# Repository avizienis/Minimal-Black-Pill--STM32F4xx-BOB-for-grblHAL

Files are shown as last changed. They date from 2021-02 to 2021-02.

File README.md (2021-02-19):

# Minimal Black Pill (STM32F4xx) BOB for grblHAL 
Single layer breakout board for the popular Black Pill (*NOT Blue Pill*). Features 4 axes, 5V outputs, optoisolated inputs.

Firmware: [grblHAL](https://github.com/terjeio/grblHAL)

The goal of this project was to replace a classical Grbl setup on an Arduino Uno/Nano, with minimal effort and minimal features (which is enough for most hobby machines anyway).
All inputs are mapped to one side of the board, all outputs (except spindle PWM) are on the other. 
This allows for a very clean single sided design and is very suitable milling, UV exposing or even toner transfer methods.
The only critical requirements for manufacturing - minimal separation between traces is 0.2mm.

## Feb 2021 Initial release
  * 4 Axis outputs
  * 10 5V buffered outputs (XYZA step/dir outputs, single source-multiple buffered outputs enable, spindle PWM and enable, mist, flood)  
  * 8 Opto-isolated inputs (mapped to XYZ limits, probe, halt, pause, start, safety door)
  * External supply connectors. Can be powered by USB, external 5V or external 12V-24V (depending on the Vreg). 
  * All I/O done on 3.5mm pitch connectors.
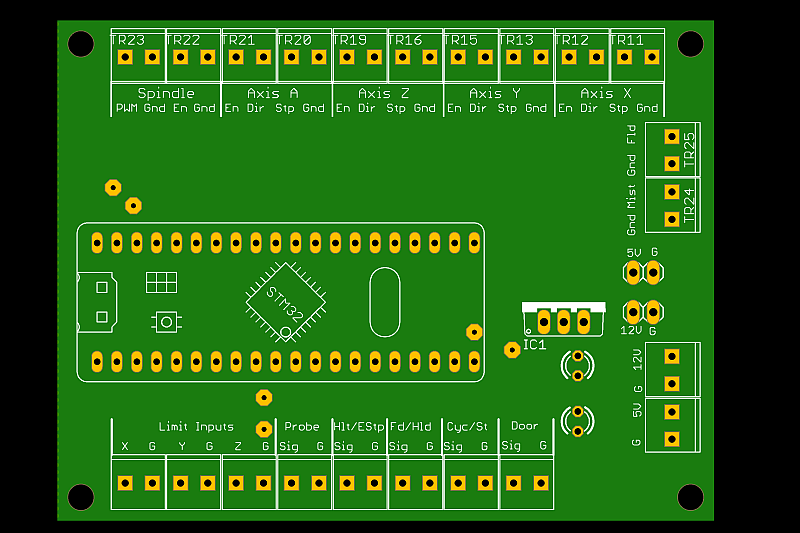
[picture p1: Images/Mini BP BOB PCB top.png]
Top view

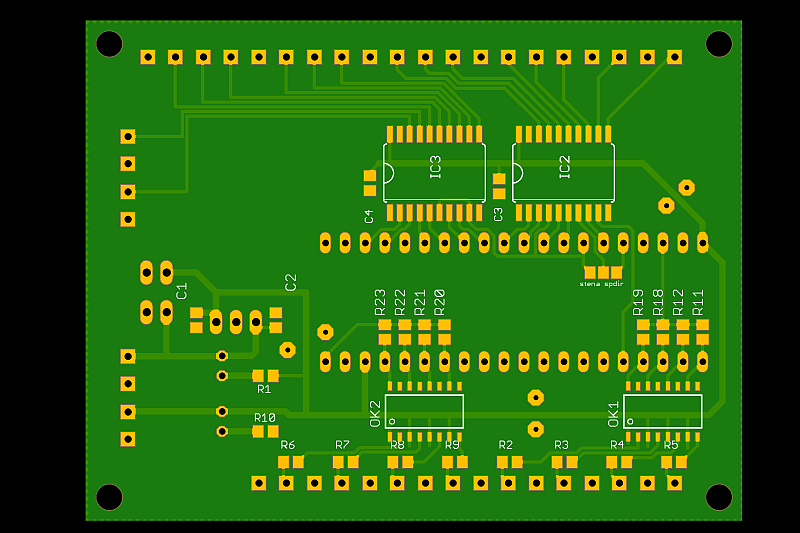
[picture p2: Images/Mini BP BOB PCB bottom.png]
Bottom view

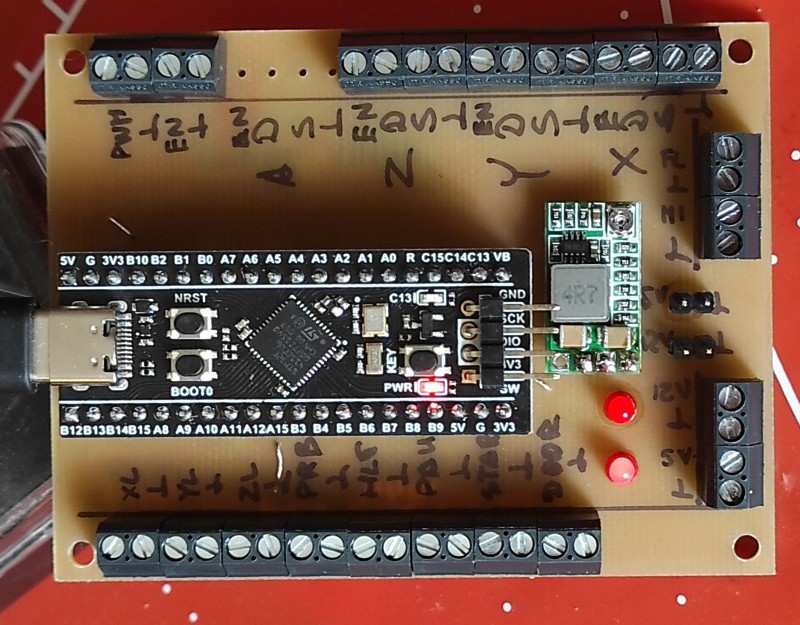
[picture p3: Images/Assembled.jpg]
Assembled

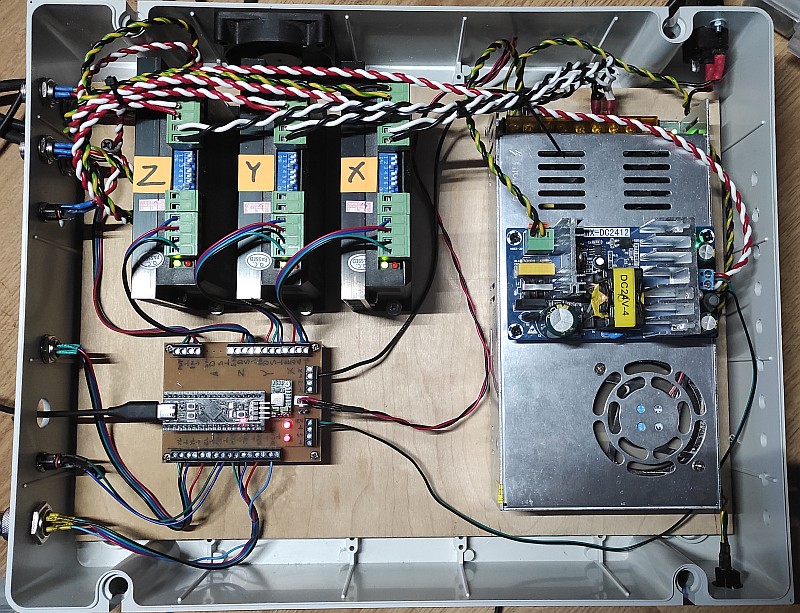
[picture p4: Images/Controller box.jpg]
Control box


## Notes

### Vreg can be a simple 7805 or as in my implementation (also see images folder) - a tiny DC-DC converter. The latter happily accepts up to 24V input.
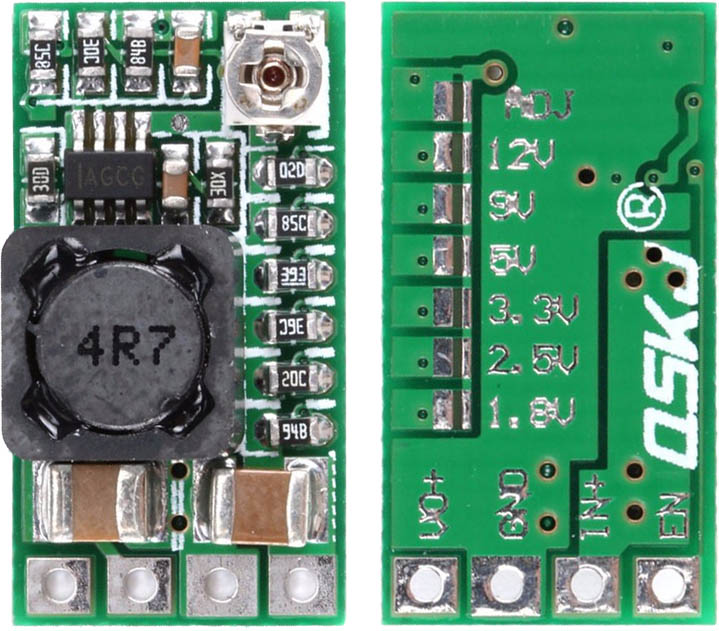
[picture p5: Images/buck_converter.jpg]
DC-DC converter


### This is only tested on genuine [WeAct Black Pill V3](https://github.com/WeActTC/MiniF4-STM32F4x1).
Other/older versions of the board can have slightly different mappings.
Also I've read that blocking USB power diodes are not present on some older variants of the board.
If so, when using external supply microcontroller's 5V lines should not be connected to the main board.

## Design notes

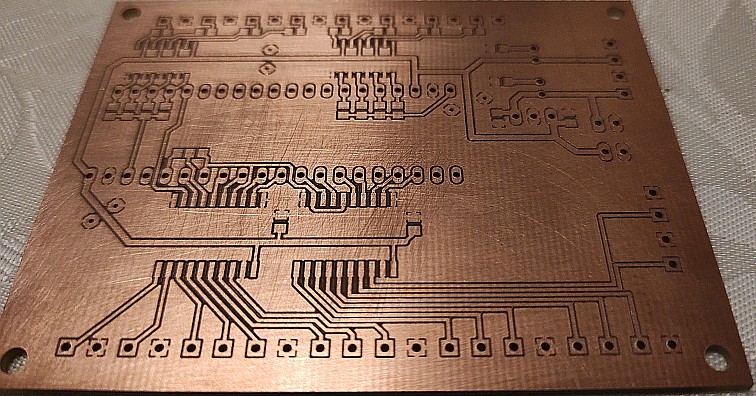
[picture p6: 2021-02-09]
Images/milled_pcb.jpg

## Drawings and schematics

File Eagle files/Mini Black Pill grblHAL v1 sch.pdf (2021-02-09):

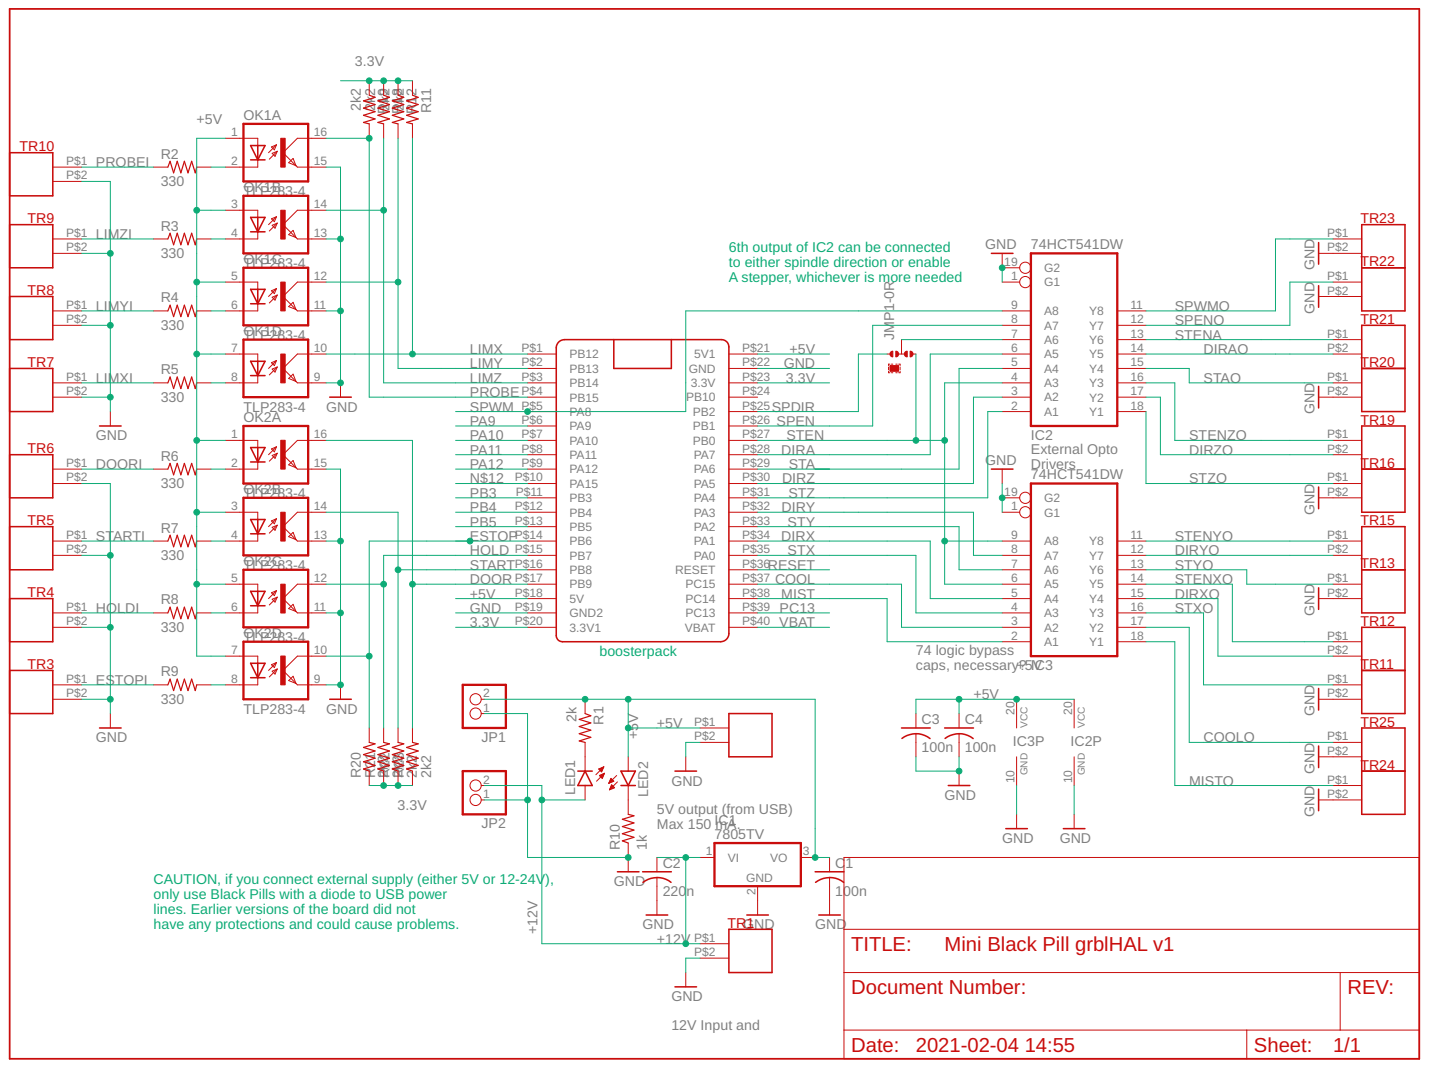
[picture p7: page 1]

6th output of IC2 can be connected
to either spindle direction or enable A stepper, whichever is more needed

CAUTION, if you connect external supply (either 5V or 12-24V), only use Black Pills with a diode to USB power

lines. Earlier versions of the board did not
have any protections and could cause problems.

Mini Black Pill grblHAL v1

Document Number: | REV:

Date: 2021-02-04 14:55 | Sheet: 1/1

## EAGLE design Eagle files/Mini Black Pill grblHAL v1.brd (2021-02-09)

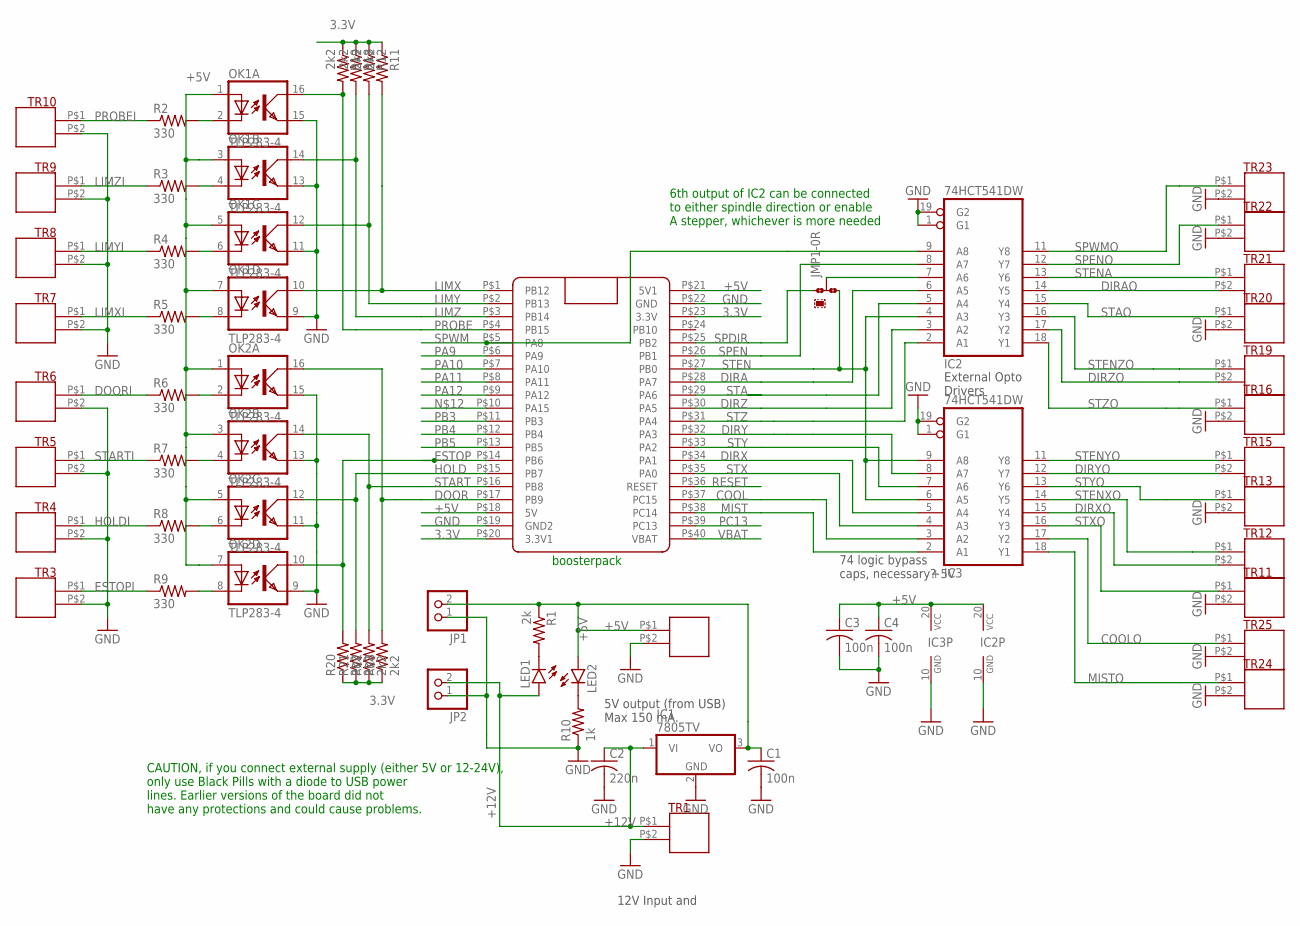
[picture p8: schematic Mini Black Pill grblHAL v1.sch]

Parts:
C1, C3, C4: 100n; C0805
C2: 220n; C0805
IC1: 7805TV; TO220V
IC2, IC3: 74HCT541DW; SO20W
JMP1: 0R-JUMPA; A0R-JMP
JP1, JP2: PINHD-1X2; 1X02
LED1, LED2: LED3MM
OK1, OK2: TLP283-4; MINI-FLAT-16
R1: 2k; R0805
R2, R3, R4, R5, R6, R7, R8, R9: 330; R0805
R10: 1k; R0805
R11, R12, R18, R19, R20, R21, R22, R23: 2k2; R0805
TR1, TR2, TR3, TR4, TR5, TR6, TR7, TR8, TR9, TR10, TR11, TR12, TR13, TR15, TR16, TR19, TR20, TR21, TR22, TR23, TR24, TR25: T35-2
U$2: BLACK_PILL; BLUE_PILL

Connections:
3.3V: R11.1, R12.1, R18.1, R19.1, R20.1, R21.1, R22.1, R23.1, U$2.P$20 (3.3V1), U$2.P$23 (3.3V)
+5V: C1.1, C3.1, C4.1, IC1.3 (VO), IC2.20 (VCC), IC3.20 (VCC), JP1.2, LED2.A, OK1.1 (A), OK1.3 (A), OK1.5 (A), OK1.7 (A), OK2.1 (A), OK2.3 (A), OK2.5 (A), OK2.7 (A), R1.1, TR2.P$1, U$2.P$18 (5V), U$2.P$21 (5V1)
+12V: C2.1, IC1.1 (VI), JP2.2, LED1.A, TR1.P$1
COOL: IC3.3 (A2), U$2.P$37 (PC15)
COOLO: IC3.17 (Y2), TR25.P$1
DIRA: IC2.6 (A5), U$2.P$28 (PA7)
DIRAO: IC2.14 (Y5), TR21.P$2
DIRX: IC3.5 (A4), U$2.P$34 (PA1)
DIRXO: IC3.15 (Y4), TR12.P$2
DIRY: IC3.8 (A7), U$2.P$32 (PA3)
DIRYO: IC3.12 (Y7), TR15.P$2
DIRZ: IC2.3 (A2), U$2.P$30 (PA5)
DIRZO: IC2.17 (Y2), TR19.P$2
DOOR: OK2.16 (COL), R23.2, U$2.P$17 (PB9)
DOORI: R6.1, TR6.P$1
ESTOP: OK2.10 (COL), R20.2, U$2.P$14 (PB6)
ESTOPI: R9.1, TR3.P$1
GND: C1.2, C2.2, C3.2, C4.2, IC1.2 (GND), IC2.1 (G1), IC2.10 (GND), IC2.19 (G2), IC3.1 (G1), IC3.10 (GND), IC3.19 (G2), JP1.1, JP2.1, OK1.9 (EMIT), OK1.11 (EMIT), OK1.13 (EMIT), OK1.15 (EMIT), OK2.9 (EMIT), OK2.11 (EMIT), OK2.13 (EMIT), OK2.15 (EMIT), R10.1, TR1.P$2, TR2.P$2, TR3.P$2, TR4.P$2, TR5.P$2, TR6.P$2, TR7.P$2, TR8.P$2, TR9.P$2, TR10.P$2, TR11.P$2, TR13.P$2, TR16.P$2, TR20.P$2, TR22.P$2, TR23.P$2, TR24.P$2, TR25.P$2, U$2.P$19 (GND2), U$2.P$22 (GND)
HOLD: OK2.12 (COL), R21.2, U$2.P$15 (PB7)
HOLDI: R8.1, TR4.P$1
LIMX: OK1.10 (COL), R11.2, U$2.P$1 (PB12)
LIMXI: R5.1, TR7.P$1
LIMY: OK1.12 (COL), R12.2, U$2.P$2 (PB13)
LIMYI: R4.1, TR8.P$1
LIMZ: OK1.14 (COL), R18.2, U$2.P$3 (PB14)
LIMZI: R3.1, TR9.P$1
MIST: IC3.2 (A1), U$2.P$38 (PC14)
MISTO: IC3.18 (Y1), TR24.P$1
unnamed: OK2.2 (C), R6.2
unnamed: LED2.K (C), R10.2
unnamed: OK2.4 (C), R7.2
unnamed: LED1.K (C), R1.2
unnamed: OK2.6 (C), R8.2
unnamed: OK1.8 (C), R5.2
unnamed: OK1.6 (C), R4.2
unnamed: OK1.4 (C), R3.2
unnamed: OK1.2 (C), R2.2
unnamed: OK2.8 (C), R9.2
unnamed: IC2.7 (A6), JMP1.2
PA9: U$2.P$6 (PA9)
PA10: U$2.P$7 (PA10)
PA11: U$2.P$8 (PA11)
PA12: U$2.P$9 (PA12)
PB3: U$2.P$11 (PB3)
PB4: U$2.P$12 (PB4)
PB5: U$2.P$13 (PB5)
PC13: U$2.P$39 (PC13)
PROBE: OK1.16 (COL), R19.2, U$2.P$4 (PB15)
PROBEI: R2.1, TR10.P$1
RESET: U$2.P$36 (RESET)
SPDIR: JMP1.1, U$2.P$25 (PB2)
SPEN: IC2.8 (A7), U$2.P$26 (PB1)
SPENO: IC2.12 (Y7), TR22.P$1
SPWM: IC2.9 (A8), U$2.P$5 (PA8)
SPWMO: IC2.11 (Y8), TR23.P$1
STA: IC2.5 (A4), U$2.P$29 (PA6)
STAO: IC2.15 (Y4), TR20.P$1
START: OK2.14 (COL), R22.2, U$2.P$16 (PB8)
STARTI: R7.1, TR5.P$1
STEN: IC2.4 (A3), IC3.6 (A5), IC3.9 (A8), JMP1.3, U$2.P$27 (PB0)
STENA: IC2.13 (Y6), TR21.P$1
STENXO: IC3.14 (Y5), TR12.P$1
STENYO: IC3.11 (Y8), TR15.P$1
STENZO: IC2.16 (Y3), TR19.P$1
STX: IC3.4 (A3), U$2.P$35 (PA0)
STXO: IC3.16 (Y3), TR11.P$1
STY: IC3.7 (A6), U$2.P$33 (PA2)
STYO: IC3.13 (Y6), TR13.P$1
STZ: IC2.2 (A1), U$2.P$31 (PA4)
STZO: IC2.18 (Y1), TR16.P$1
VBAT: U$2.P$40 (VBAT)

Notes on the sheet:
External Opto Drivers
74 logic bypass caps, necessary?
boosterpack
5V output (from USB) Max 150 mA.
12V Input and
6th output of IC2 can be connected to either spindle direction or enable A stepper, whichever is more needed
CAUTION, if you connect external supply (either 5V or 12-24V), only use Black Pills with a diode to USB power lines. Earlier versions of the board did not have any protections and could cause problems.

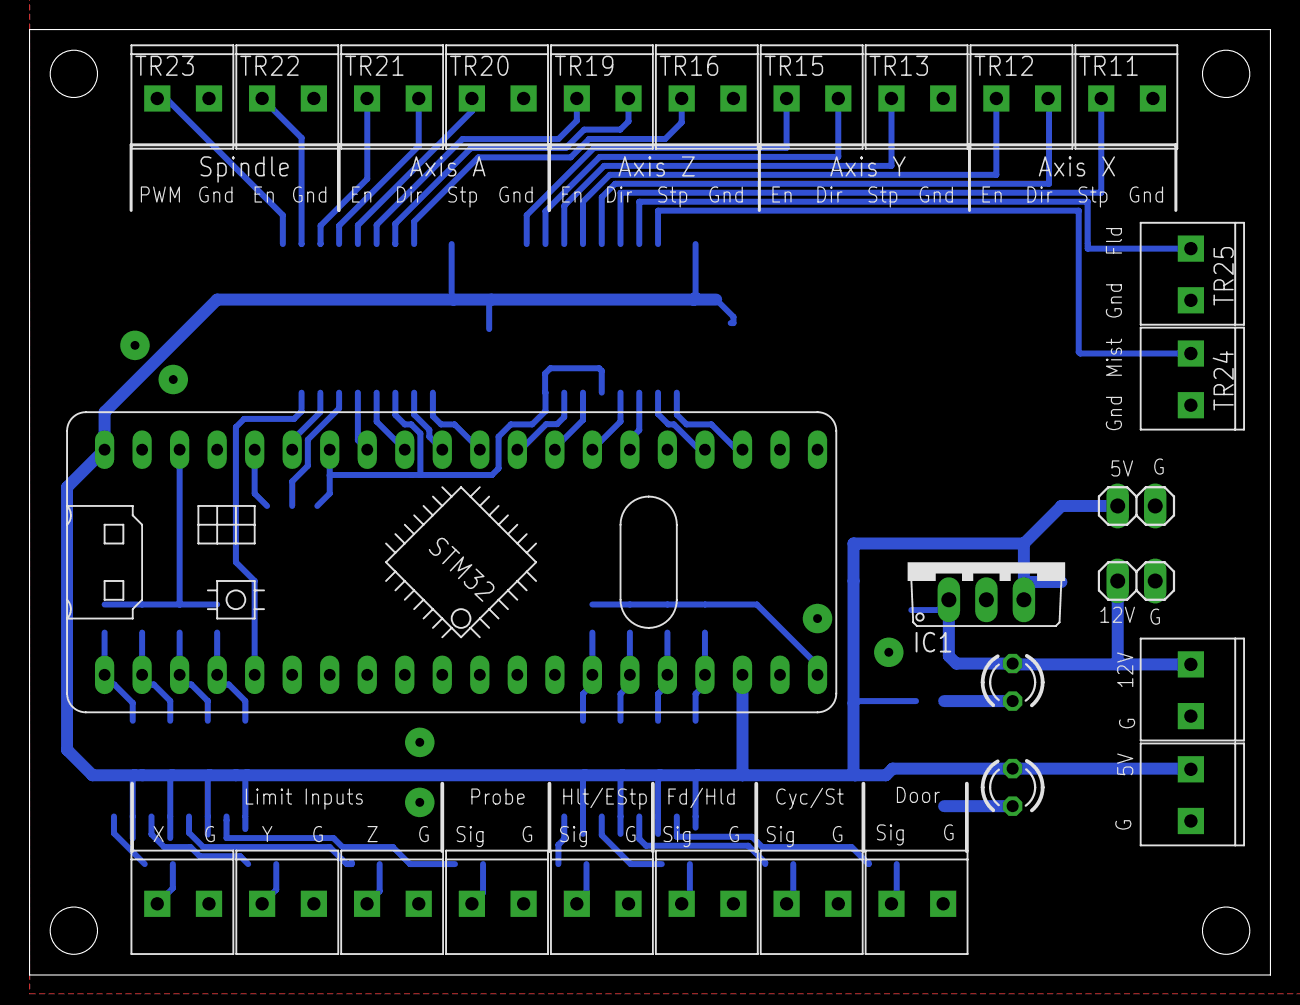
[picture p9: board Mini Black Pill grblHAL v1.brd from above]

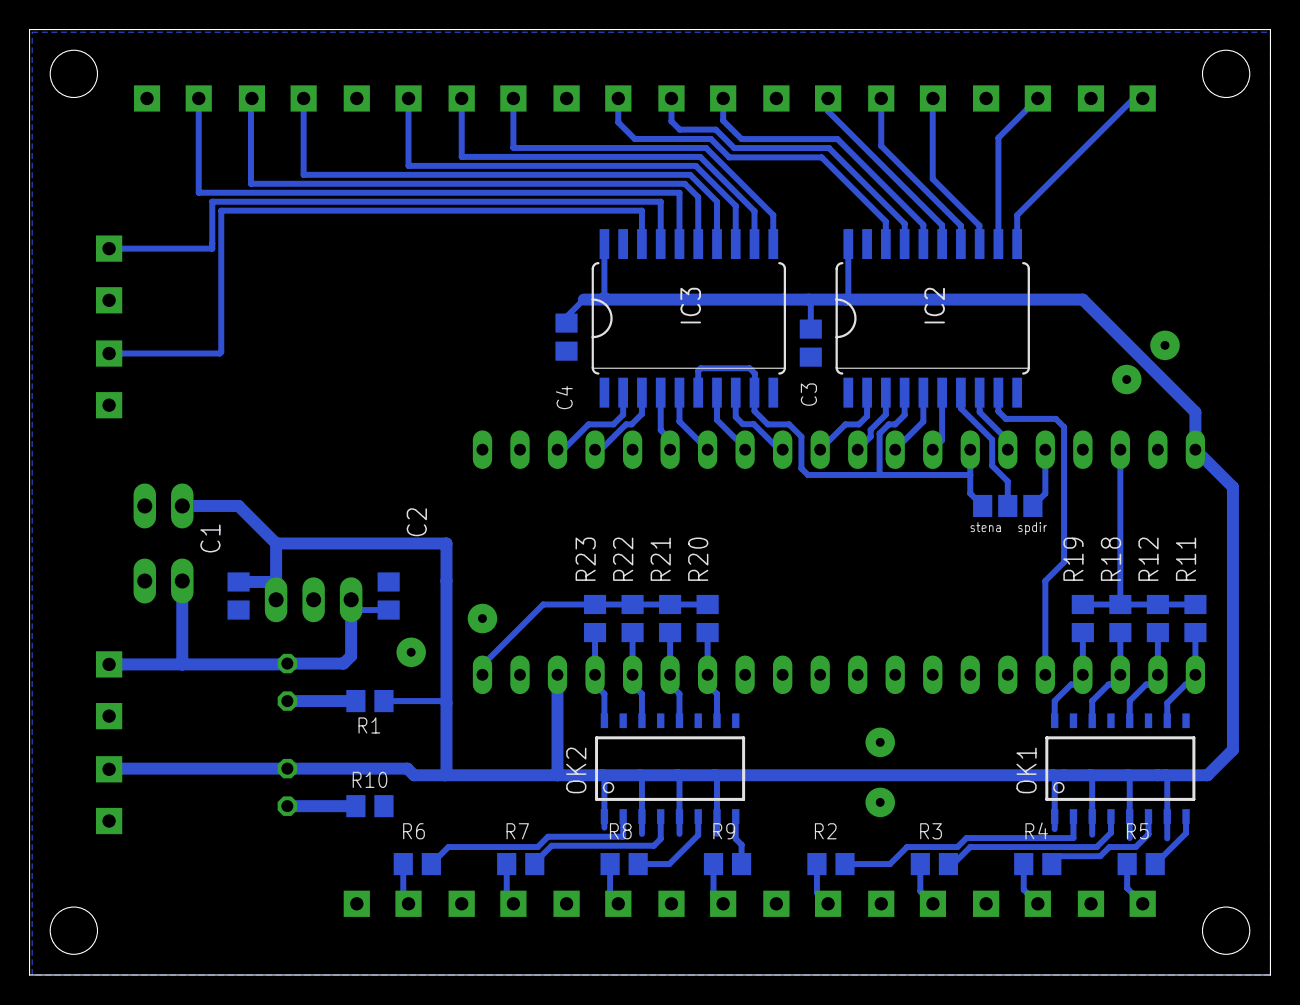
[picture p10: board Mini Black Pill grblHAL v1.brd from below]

Board: 2 copper layers, 84.0 x 64.0 mm, 55 parts (27 on the bottom side), 61 nets.

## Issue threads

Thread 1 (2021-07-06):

Feature Request

marlboro, 2021-07-06:
First, I love what you have done here! It looks really nice and I was wondering how is it working for you? Also, I have a couple of wish list items I wanted to throw out there for you:
1. Can you upgrade this design to support up to a 48V power supply?  I will be using a 36V in the beginning.
2. I like the idea of a USB Type B connector on the outside of my enclosure (like you see on most USB controller boxes).  I think it would be awesome if there was an optional USB Type B connector that could be soldered onto the board if desired.  Perhaps located on the left or right beside the STM32.

Best,
Mel

avizienis, 2021-07-07:
Hi, thanks! It's been in operations for the last 6 months or so. I'm only using my CNC for casual hobby cutting but still, the board is stable. I have no immediate plans to upgrade/develop this board but feel free to fork the design and improve!
Regarding 48V, it boils down to using a stepdown converter that accepts such high input voltage. Since abundant ready made modules are available, just use one of those. I see no point in implementing a buck converter on the PCB itself.
As for B connector, I would use (and have used in previous projects) this:
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
There are many variations available as well

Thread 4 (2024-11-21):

any feedback on this board after three years of use?

thirstyone, 2024-11-21:
it's more of a question. Is it worth replicating? Does it have any drawbacks?
Right now I am using an arduino nano running grbl, without any bob, just wires going to external stepper drivers, and i am  setting up RPMs on my spindle manually. I got a bit tired of that mess, so I was looking for some open-source grbl-hal solution (based on some preferably low price boards available through aliexpress). But to my surprise, most of the boards on the market are commercial products, and only few of them have published board layout (so that I could order them from a pcb house).
Besides, many of them come with embedded drivers (which I don't need).

What would you say about EMI resistance of your BOB? (It doesn't have any ground polygons, besides, the tracks are thin and close to each other
Yet one more thing: since i have a VFD to control my spindle, and it supports rs485, it somewhat makes sense to me to use this interface instead of voltage or PWM control, right? (moreover, as far as I remember, grbl-hal allows to do so).

So, all in all, after three years of usage, is there anything you'd like to change/improve on your board?

avizienis, 2024-11-22:
Hi, the board works fine but it's not as polished as some other offerings, especially since you need features like rs485. If I were to do it all again, I'd just buy a board from one of the community members on Etsy

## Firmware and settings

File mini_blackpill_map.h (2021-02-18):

/*
  cnc_boosterpack_map.h - driver code for STM32F4xx processor (on Blackpill board)

  Part of GrblHAL

  Copyright (c) 2020 Terje Io

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
  You should have received a copy of the GNU General Public License
  along with Grbl.  If not, see <http://www.gnu.org/licenses/>.
*/

#define BOARD_NAME "Minimal BlackPill grblHAL"

#ifdef EEPROM_ENABLE
#undef EEPROM_ENABLE
#endif

#ifdef CNC_BLACKPILL
#undef CNC_BLACKPILL
#endif

#define CNC_BLACKPILL 1
#define EEPROM_ENABLE   0 // Disabled for now for BlackPill - pin differences... // Only change if BoosterPack does not have EEPROM mounted

// Define step pulse output pins.
#define STEP_PORT       GPIOA
#define X_STEP_PIN      0
#define Y_STEP_PIN      2
#define Z_STEP_PIN      4
#define X_STEP_BIT      (1<<X_STEP_PIN)
#define Y_STEP_BIT      (1<<Y_STEP_PIN)
#define Z_STEP_BIT      (1<<Z_STEP_PIN)
#if N_AXIS > 3
#define A_STEP_PIN      6
#define A_STEP_BIT      (1<<A_STEP_PIN)
#define STEP_MASK       (X_STEP_BIT|Y_STEP_BIT|Z_STEP_BIT|A_STEP_BIT) // All step bits
#else
#define STEP_MASK       (X_STEP_BIT|Y_STEP_BIT|Z_STEP_BIT) // All step bits
#endif
#define STEP_OUTMODE    GPIO_MAP

// Define step direction output pins.
#define DIRECTION_PORT      GPIOA
#define X_DIRECTION_PIN     1
#define Y_DIRECTION_PIN     3
#define Z_DIRECTION_PIN     5
#define X_DIRECTION_BIT     (1<<X_DIRECTION_PIN)
#define Y_DIRECTION_BIT     (1<<Y_DIRECTION_PIN)
#define Z_DIRECTION_BIT     (1<<Z_DIRECTION_PIN)
#if N_AXIS > 3
#define A_DIRECTION_PIN     7
#define A_DIRECTION_BIT     (1<<A_DIRECTION_PIN)
#define DIRECTION_MASK      (X_DIRECTION_BIT|Y_DIRECTION_BIT|Z_DIRECTION_BIT|A_DIRECTION_BIT) // All direction bits
#else
#define DIRECTION_MASK      (X_DIRECTION_BIT|Y_DIRECTION_BIT|Z_DIRECTION_BIT) // All direction bits
#endif
#define DIRECTION_OUTMODE   GPIO_MAP

// Define stepper driver enable/disable output pin.
#define STEPPERS_DISABLE_PORT   GPIOB
#define STEPPERS_DISABLE_PIN    0
#define STEPPERS_DISABLE_BIT    (1<<STEPPERS_DISABLE_PIN)
#define STEPPERS_DISABLE_MASK   STEPPERS_DISABLE_BIT

// Define homing/hard limit switch input pins.
#define LIMIT_PORT       GPIOB
#define X_LIMIT_PIN      12
#define Y_LIMIT_PIN      13
#define Z_LIMIT_PIN      14
#define X_LIMIT_BIT      (1<<X_LIMIT_PIN)
#define Y_LIMIT_BIT      (1<<Y_LIMIT_PIN)
#define Z_LIMIT_BIT      (1<<Z_LIMIT_PIN)
#if N_AXIS > 3
#define A_LIMIT_PIN      15
#define A_LIMIT_BIT      (1<<A_LIMIT_PIN)
#define LIMIT_MASK       (X_LIMIT_BIT|Y_LIMIT_BIT|Z_LIMIT_BIT|A_LIMIT_BIT) // All limit bits
#else
#define LIMIT_MASK       (X_LIMIT_BIT|Y_LIMIT_BIT|Z_LIMIT_BIT) // All limit bits
#endif
#define LIMIT_INMODE GPIO_SHIFT12

  // Define spindle enable and spindle direction output pins.
#define SPINDLE_ENABLE_PORT         GPIOB
#define SPINDLE_ENABLE_PIN          1
#define SPINDLE_ENABLE_BIT          (1<<SPINDLE_ENABLE_PIN)
#define SPINDLE_DIRECTION_PORT      GPIOB
#define SPINDLE_DIRECTION_PIN       2
#define SPINDLE_DIRECTION_BIT       (1<<SPINDLE_DIRECTION_PIN)

// Define spindle PWM output pin.
#define SPINDLE_PWM_PORT            GPIOA
#define SPINDLE_PWM_PIN             8
#define SPINDLE_PWM_BIT             (1<<SPINDLE_PWM_PIN)

// Define flood and mist coolant enable output pins.
#define COOLANT_FLOOD_PORT          GPIOC
#define COOLANT_FLOOD_PIN           15
#define COOLANT_FLOOD_BIT           (1<<COOLANT_FLOOD_PIN)
#define COOLANT_MIST_PORT           GPIOC
#define COOLANT_MIST_PIN            14
#define COOLANT_MIST_BIT            (1<<COOLANT_MIST_PIN)

// Define user-control controls (cycle start, reset, feed hold) input pins.
#define CONTROL_PORT                GPIOB
#define CONTROL_RESET_PIN           6
#define CONTROL_FEED_HOLD_PIN       7
#define CONTROL_CYCLE_START_PIN     8
#define CONTROL_SAFETY_DOOR_PIN     9
#define CONTROL_INMODE GPIO_SHIFT6

#define CONTROL_RESET_BIT           (1<<CONTROL_RESET_PIN)
#define CONTROL_FEED_HOLD_BIT       (1<<CONTROL_FEED_HOLD_PIN)
#define CONTROL_CYCLE_START_BIT     (1<<CONTROL_CYCLE_START_PIN)
#define CONTROL_SAFETY_DOOR_BIT     (1<<CONTROL_SAFETY_DOOR_PIN)
#define CONTROL_MASK                (CONTROL_RESET_BIT|CONTROL_FEED_HOLD_BIT|CONTROL_CYCLE_START_BIT|CONTROL_SAFETY_DOOR_BIT)

// Define probe switch input pin.
#define PROBE_PORT                  GPIOB
#define PROBE_PIN                   15
#define PROBE_BIT                   (1<<PROBE_PIN)

#if KEYPAD_ENABLE
#error Keypad not supported
#define KEYPAD_PORT                 GPIOB
#define KEYPAD_STROBE_PIN           15
#define KEYPAD_STROBE_BIT           (1<<KEYPAD_STROBE_PIN)
#endif

#if SDCARD_ENABLE
#error SDcard not supported
#define SD_CS_PORT  GPIOA
#define SD_CS_PIN   3
#define SD_CS_BIT   (1<<SD_CS_PIN)
#endif

/* EOF */

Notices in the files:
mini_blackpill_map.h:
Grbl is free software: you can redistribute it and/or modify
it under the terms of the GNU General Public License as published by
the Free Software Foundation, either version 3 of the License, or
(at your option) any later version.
